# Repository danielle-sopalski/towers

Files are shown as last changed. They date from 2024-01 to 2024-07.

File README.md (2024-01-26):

# Miniature, Modular, Indoor Grow Towers

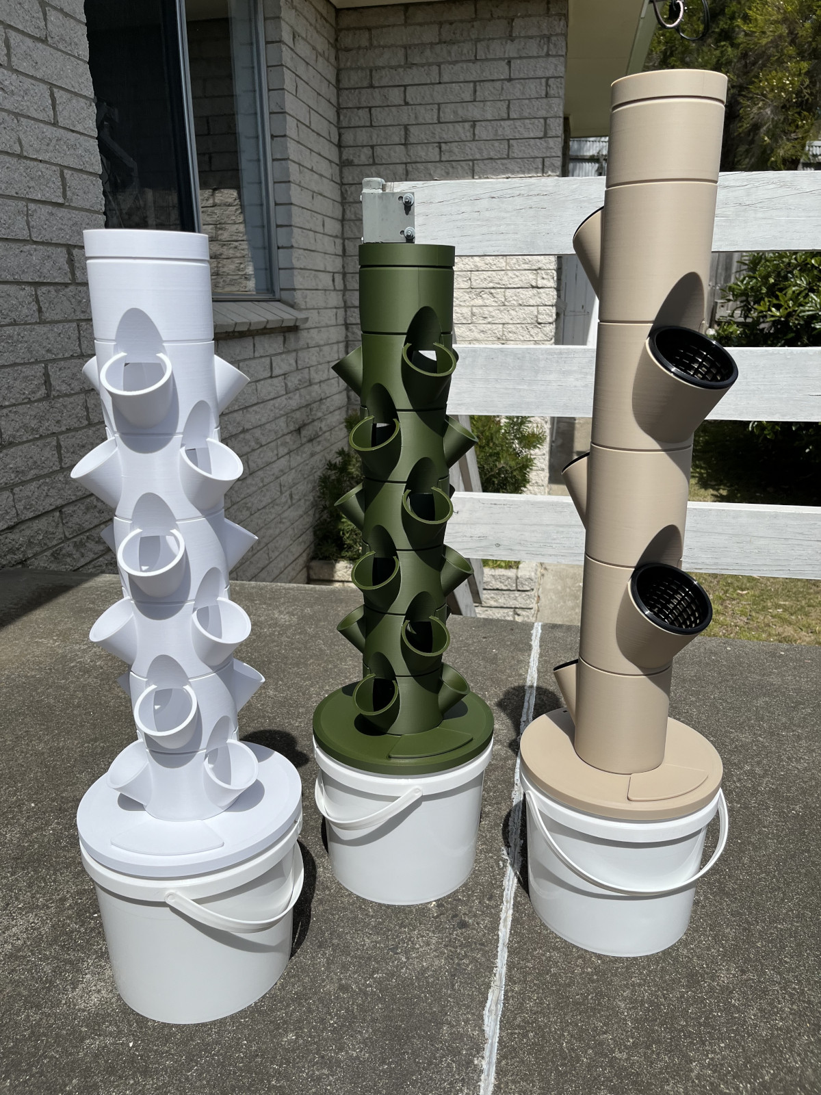
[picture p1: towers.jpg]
Image of three grow towers


## What is this?

These are hydroponic[^1] grow towers! The concept isn't new, and it's pretty straightforward: Instead of planting in soil, you plant in a loose medium like perlite or coco peat. Rather than the plants deriving nutrients from the growing medium, nutrients are dissolved in water, and that water is circulated through the system to deliver moisture and nutrients to the plants' roots. Because the water is recirculated and delivered directly to plants' roots, grow towers can be extremely water-efficient! Because nutrients are dissolved in the water itself, it's easy to control exactly what you put into the system, which means you can tailor it to the needs of whatever you've planted.

That said, I'm only a novice gardener, so I take a more simple approach: I use a general-purpose nutrient solution for all of my grows, and it seems to work out great for things like herbs and tomatoes! Hydroponic gardening can be as in-depth or as straightforward as you want it to be; it can be easy to start, and the complexity of the hobby can grow alongside your level of experience. :)

All of the parts in this project are designed to be 3D-printable without supports, and they're modular, meaning you can choose how many "planter" modules to put together to build your tower.

The planter modules come in two varieties: modules which fit a single 80mm net-pot per module; and modules which fit three 50mm net-pots per module. These net pots are easy to find at your local hydroponics shop or online if you don't have a shop nearby. For most herbs, lettuces, and even fruiting vegetables like tomatoes and peas, I recommend starting with the 50mm modules. Whereas you would normally need to use pots large enough to contain a plant's entire root system, net pots are designed to allow the root system to grow beyond the pot and down into the tower itself, so as long as a plant's base can fit in the diameter of the pot, you're golden!

[^1]: Well, technically, they could be called *aeroponic* grow towers. The best distinction I've heard between hydroponics and aeroponics is that if the roots are exposed to air, it's an aeroponic system. In theory, you could rig up one of these towers with some 4mm micro sprays or the like instead of the provided showerhead -- or you could even forego using a pump entirely and instead place a fog generator in the reservoir to experiment with fogponics! -- but I haven't tried it myself.

## What can I grow in these?

Pretty much anything except root vegetables! Lettuces, herbs, and peas are an easy place to start. Tomatoes are pretty easy too! It could even be fun to grow ornamentals in the towers, but my primary goal is to get people growing their own food.

## How do I get started? What do I need?

First things first: **Talk to the folks at your local hydroponics shop.** They're going to know way, *way* more than me about hydroponics and about growing plants in general. They'll be able to recommend nutrient solutions, pH buffers, and tools. **More importantly, they'll likely be able to advise you about hydroponics safety.** Not only does hydroponics involve the use of some simple chemicals like acidic and alkaline solutions for balancing pH, but a hydroponics system improperly tended to can become host to unwanted pathogens. The following advice is **general** in nature.

### To get started, you'll need a few items outside of the tower itself:
#### Non-printable components:
* A submersible pump to sit in the tower reservoir.[^2] I use [Aqua One Maxi 103](https://aquaone.com.au/2015-04-16-04-47-04/filtration/pumps-2/item/2702-11321-11322-11323-11324-11325-11326) pumps in my towers, but your hydroponics shop can advise you. You'll need to compare the height of your tower to the pump's **maximum head height.** If your tower is taller than that head height, your pump will struggle to push water to the top! If the maximum head height is significantly *higher* than the height of your tower, you may end up with too much water pressure for the system to handle.
* An outlet timer to switch your pump on and off automatically.[^2] I recommend a cycle of 15 minutes on, then one hour off.
* A way to adapt your pump's outlet to 13mm tubing.
* A length of 13mm tubing equal to the distance from your pump's outlet to shower head inlet about halfway up the "chimney module" -- that's the module at the top into which the shower head is inserted.
* A bucket to serve as your system's reservoir. At the moment, the design suits only Ayva brand 5L buckets. These are an Australian make of bucket commonly available individually at Bunnings Warehouse under the brand name [Handy Pail](https://www.bunnings.com.au/handy-pail-5l-plastic-pail-with-lid_p4475883). My hope is that as people take notice of the project, folks will contribute revised bucket lid designs suitable for buckets available in countries other than Australia.
* Either 50mm or 80mm net pots. While I haven't included a design for those in this project, there are actually a [ton of available printable versions](https://thangs.com/search/net%20pot?scope=all)!

#### Tools:
* A pH meter is really important to make sure your nutrient solution is in the right pH range for your plants.
* Eyedroppers are a great way to dispense the small amounts of buffer needed to balance your nutrient solution's pH.
* A small graduated cylinder or conical medicine measure -- that's what I use -- is perfect for measuring out concentrated nutrient solution for mixing. Conical medicine measures can be found at chemists (pharmacies), and they're very inexpensive.

#### Consumables:
* Concentrated nutrient solution
* Hydroponics acid, often called "pH down"[^3]
* Hydroponics base, often called "pH up"[^3]
* It's best practice -- many would say a must -- to use a cleaning agent to sterilize your tower as much as possible before planting and filling with nutrient solution. The folks at your local hydroponics shop can advise you.
* A planting medium. I prefer perlite for its excellent drainage, but coco peat is a perfectly valid option too. Your local hydroponics shop can advise you.
* Water of course!
* Your local hydroponics shop can advise you about other additives to help keep your system healthy.

#### Optional stuff if you wanna go wild:
* A grow lamp
* A grow tent
* A little fan to help air circulate through your plants
* A trellis or trainer and twine is quite helpful for plants like peas and tomatoes.

[^2]: These towers **can** leak. Be sure to place them such that any leaks wouldn't reach electrical outlets or electrical devices.
[^3]: Remember, it's of paramount importance to exercise caution and wear appropriate personal protective equipment when handling harsh chemicals such as (but not limited to) acids, bases, and oxidizing agents.

### How many modules should I use?
I recommend starting with just one or two of the 50mm planter modules. Each 50mm module will give you three net-pot receptacles, and you may be surprised by how much water your chosen plants will consume once they reach a decent size. One of the limitations of these towers as they are is the reservoir size. At 5L, the reservoir can be drained pretty quickly by a fully populated, reasonably tall tower! However, I've also provided what I'm calling a ["bulkhead fitting"](https://github.com/danielle-sopalski/towers/blob/main/bucket%20lid/Bulkhead%20for%20Larger%20Systems.step), which can be fastened with screws to larger reservoir lids as an alternative to the printable bucket lid for those who want to try building larger systems (or even systems with multiple towers attached to the same large reservoir).

### Once you have everything you need, be sure to check out the [assembly manual](https://github.com/danielle-sopalski/towers/blob/main/manual/main.pdf). It's not yet complete -- a couple of sections are filled with *Lorem ipsum* -- but it contains complete assembly instructions, and I've put a lot of effort into making wireframe diagrams that I hope will help!

## Printing Recommendations

The towers were designed to be printed by my Bambu Lab P1S printer, but they should be printable on any decent FDM printer, maybe with some tweaking of clearances.

**All parts are designed to be printed without supports.** Examples of recommended print orientation can be found in the example 3MF files. When printed with the recommended orientation and on a print surface such as textured PEI, the result should be a nice, textured finish on all upward-facing surfaces of the assembled tower. :)

For parts with little surface area contacting the print bed, eg planter modules, an inner brim can be used to promote bed adhesion.

I recommend using PLA+ and **strongly** recommend you find **food-grade** filament to print with.[^4]

Generally, I've been printing with:
* 0.28mm layer height
* 0.4mm nozzle, though 0.6mm or larger certainly isn't out of the question!
* 3 wall loops for planter modules; 6 wall loops for the bucket lid
* 3 top and bottom shell layers
* Rectilinear top and bottom surface pattern for the bucket lid; concentric top and rectilinear bottom surface pattern for the planter modules, bucket lid cap, bucket lid lock-ring, bucket lid cable glands, tower chimney, chimney lid
* **No supports**
* Gyroid infill, 15%

[^4]: Remember: Just because your filament is food-grade doesn't mean your printer or finished prints are!

## Intention

This is a project I've been working on for a little while with the intention, up until now, of starting a small business centered around hyper-local manufacturing of goods. The hope was to promote the idea of "garage factories," tiny print farms in people's spare space serving local communities with goods that would otherwise need to be sourced from large factories far away. Truth be told, though, I'm not a business person, and I don't think I want to move forward with it myself -- or at least not alone -- so I'm opening the project in the hope that others will see value in it and contribute their time and abilities to making it better than I ever could by myself.

My hope now is that folks will go about producing these grow towers for their own local communities, promoting both hyper-local manufacturing and home-grown produce.

## What's Here

These are small, modular, indoor, hydroponic grow towers made to sit in a living room or by a window. Included in the repo are:
* A variant with one 80mm net-pot receptacle per module: Fusion 360, STEP
* A variant with three 50mm net-pot receptacles per module: Fusion 360, STEP
* A mostly-complete (though certainly not perfectly written) user manual: PDF, (badly written) LaTeX; A4 format as well as A5 booklet format
* Wireframe diagrams of all parts and assembly steps: SVG
* 3MF files of all parts offering example printing parameters.

## What Needs to Be Done

A number of things need improvement:
* The manual needs an introduction, a sensible list of precautions, cleaning and maintenance recommendations, and general proofreading and refinement.
* The Fusion 360 files need to be cleaned up. I'm bad at keeping things organized while I work.
* **The current design only suits a common Australian brand of 5L bucket.** I'd love it if folks could contribute revised versions that suit buckets available in other parts of the world.
* We need a good open-source license that allows individuals to freely produce and sell these towers while excluding large manufacturers, corporations, and the wealthy. For now, I'm opting for the [Creative Commons Attribution-NonCommercial-ShareAlike 4.0 International license](https://creativecommons.org/licenses/by-nc-sa/4.0/).

### Models from this project are also published to [Thangs](https://thangs.com/designer/danielle.sopalski/3d-model/Dani%27s%20Miniature%20Grow%20Towers-995522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) and [Thingiverse](https://www.thingiverse.com/thing:6444781).

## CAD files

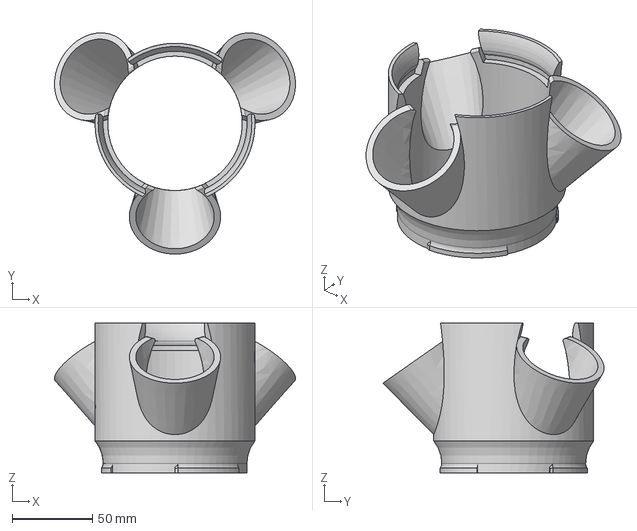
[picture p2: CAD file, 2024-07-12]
50mm/50mm Planter Base Module.step
150.6 x 138.2 x 93.6 mm

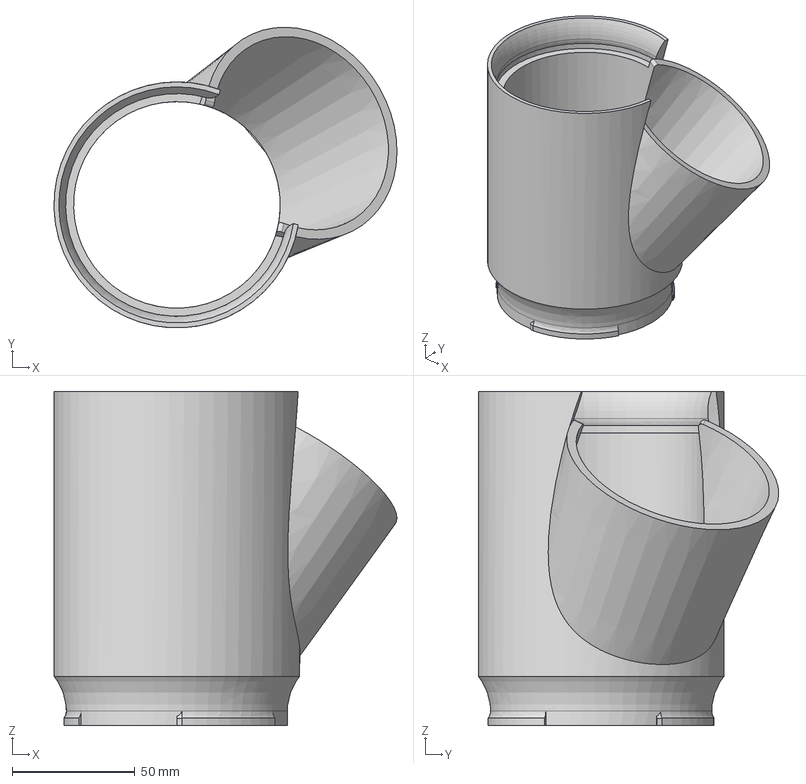
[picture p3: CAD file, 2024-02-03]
80mm/80mm Planter Base Module.step
139.5 x 122.2 x 135.9 mm

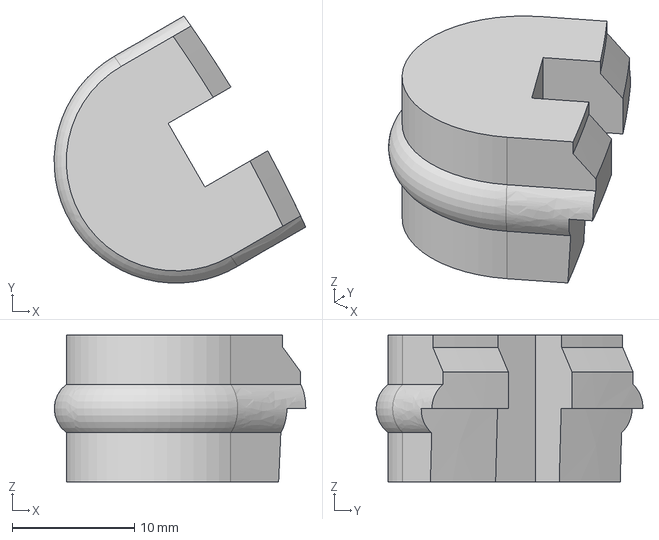
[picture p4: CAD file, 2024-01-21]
bucket lid/Ayva 5L Lock-Ring Pail Lid Cable Gland.step
20.5 x 21.8 x 12.0 mm

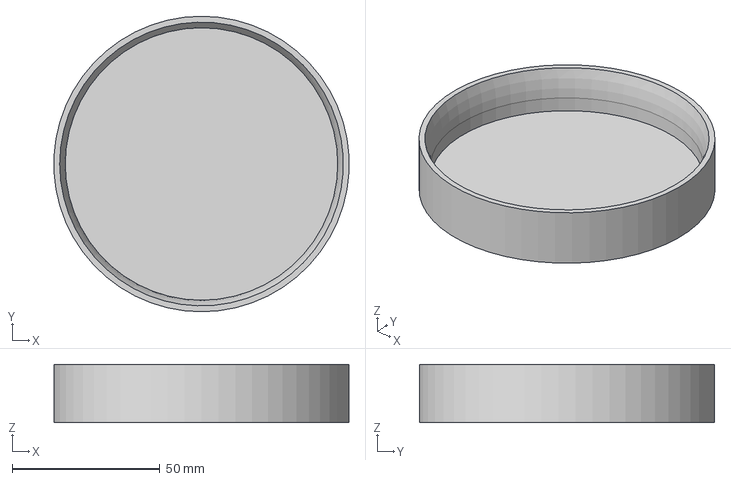
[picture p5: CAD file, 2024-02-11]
chimney lid/Chimney Lid.step
99.8 x 100.0 x 19.6 mm

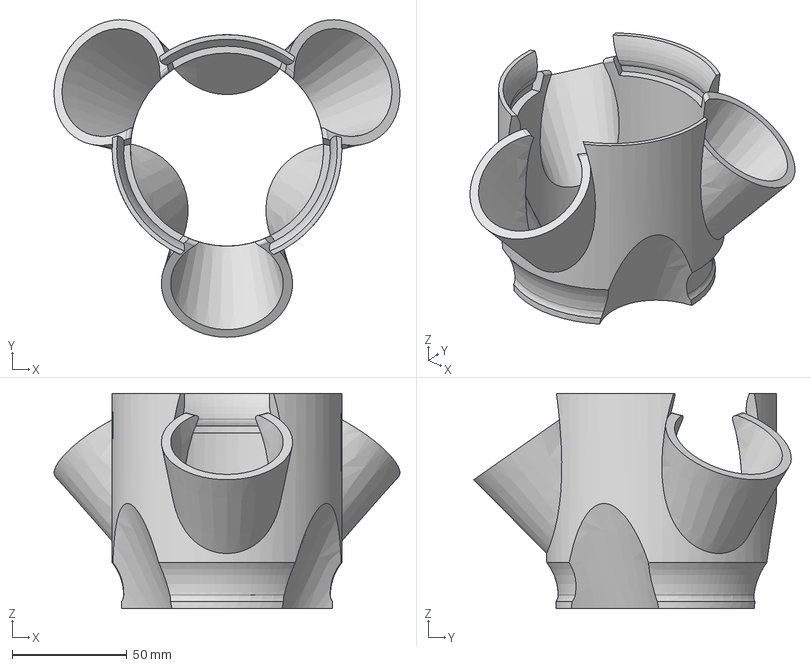
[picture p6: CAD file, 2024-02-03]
50mm/50mm Planter Module.step
150.6 x 138.2 x 93.6 mm

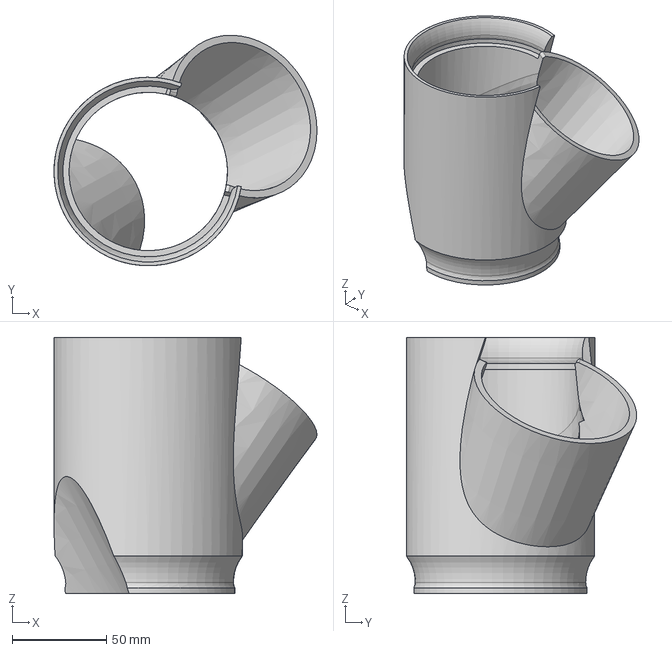
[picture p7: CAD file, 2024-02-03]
80mm/80mm Planter Module.step
139.5 x 122.2 x 135.9 mm

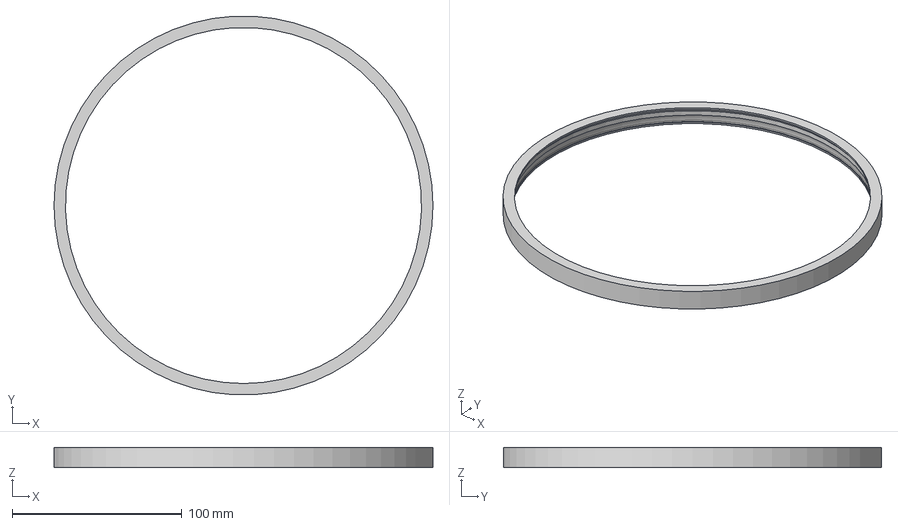
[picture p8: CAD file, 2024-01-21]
bucket lid/Ayva 5L Lock-Ring Pail Lid Lock-Ring.step
223.5 x 223.2 x 12.0 mm

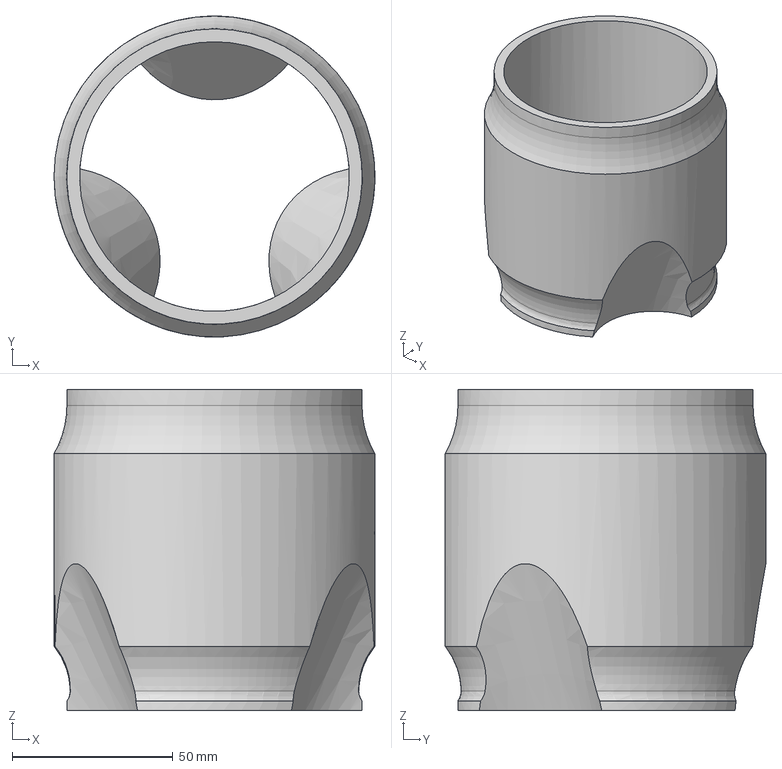
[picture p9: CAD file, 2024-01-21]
50mm/50mm Chimney Module.step
100.0 x 100.0 x 100.0 mm

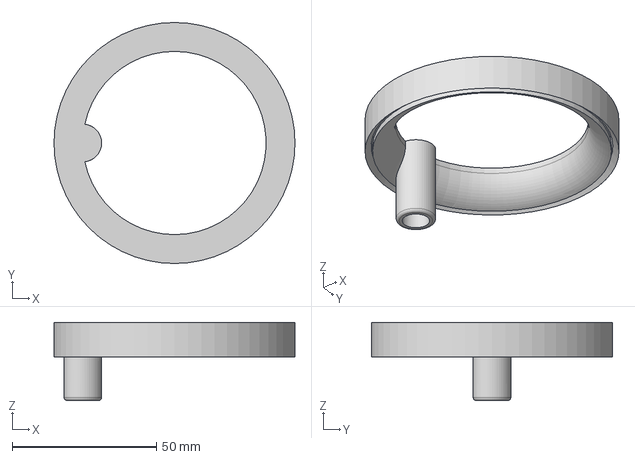
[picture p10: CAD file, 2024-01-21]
80mm/80mm Shower Head.step
83.4 x 83.4 x 27.0 mm

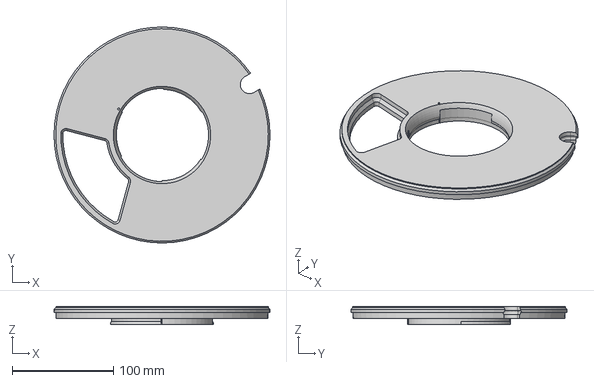
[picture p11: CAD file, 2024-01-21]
bucket lid/Ayva 5L Lock-Ring Pail Lid.step
213.3 x 213.3 x 18.0 mm

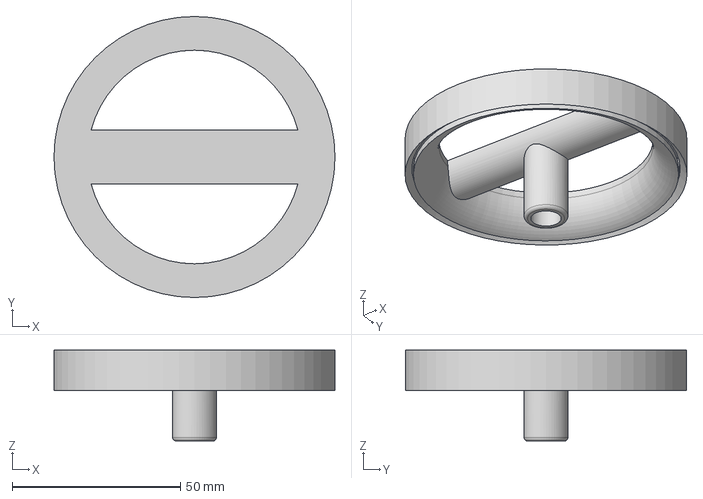
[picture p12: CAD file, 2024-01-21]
50mm/50mm Shower Head.step
83.4 x 83.4 x 27.0 mm

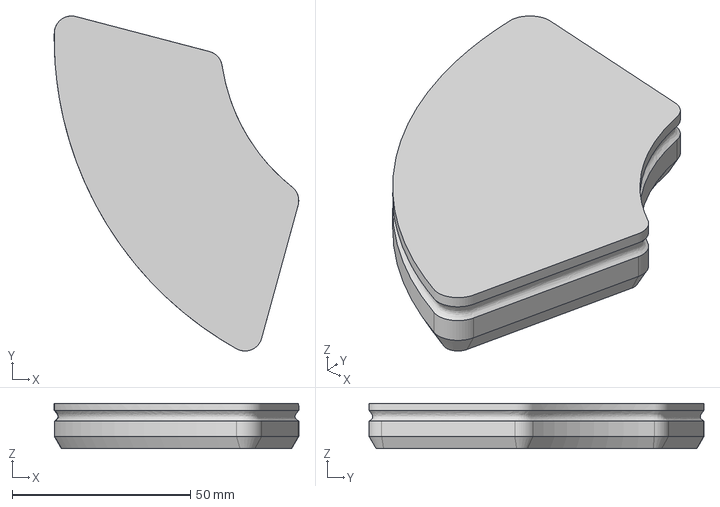
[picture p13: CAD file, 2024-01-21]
bucket lid/Ayva 5L Lock-Ring Pail Lid Cover.step
68.6 x 94.0 x 12.8 mm

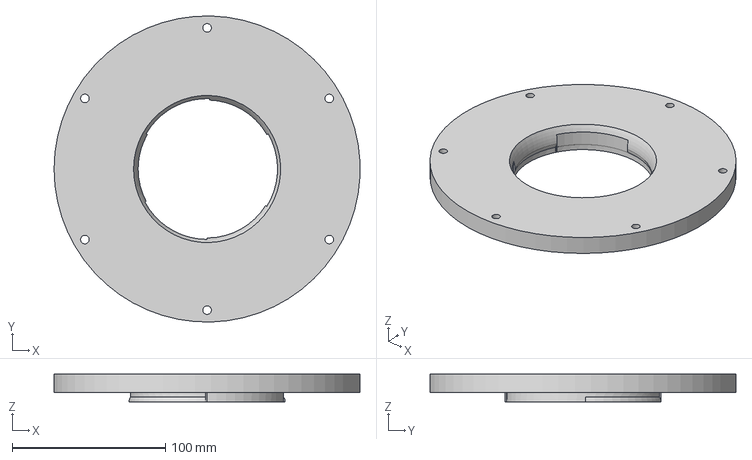
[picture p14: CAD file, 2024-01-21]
bucket lid/Bulkhead for Larger Systems.step
199.9 x 199.9 x 18.0 mm

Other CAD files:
80mm/80mm Chimney Module.step
50mm/3mf/50mm Chimney Module.3mf
50mm/3mf/50mm Planter Base Module.3mf
50mm/3mf/50mm Planter Module.3mf
50mm/3mf/50mm Shower Head.3mf
50mm/Tower 50mm.f3z
80mm/3mf/80mm Chimney Module.3mf
80mm/3mf/80mm Planter Base Module.3mf
80mm/3mf/80mm Planter Module.3mf
80mm/3mf/80mm Shower Head.3mf
80mm/Tower 80mm.f3z
bucket lid/3mf/Ayva 5L Lock-Ring Pail Lid Cable Gland.3mf
bucket lid/3mf/Ayva 5L Lock-Ring Pail Lid Cover.3mf
bucket lid/3mf/Ayva 5L Lock-Ring Pail Lid Lock-Ring.3mf
bucket lid/3mf/Ayva 5L Lock-Ring Pail Lid.3mf
chimney lid/3mf/Chimney Lid.3mf

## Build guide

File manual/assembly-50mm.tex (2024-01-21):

\subsection{Parts}

\begin{center}
    \begin{minipage}{0.3\textwidth}
        \centering
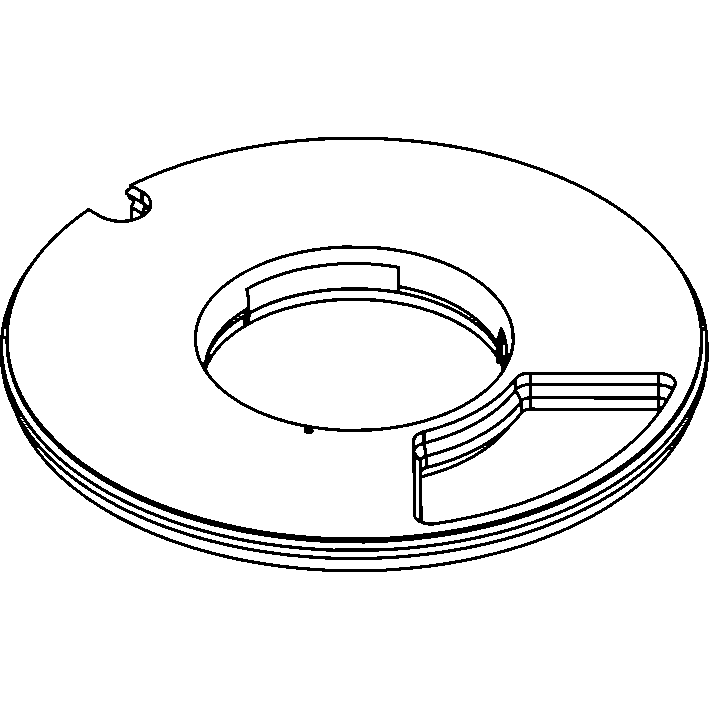
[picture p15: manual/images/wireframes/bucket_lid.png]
        
        \captionof*{figure}{1x Bucket Lid}
    \end{minipage}
    \hfill
    \begin{minipage}{0.3\textwidth}
        \centering
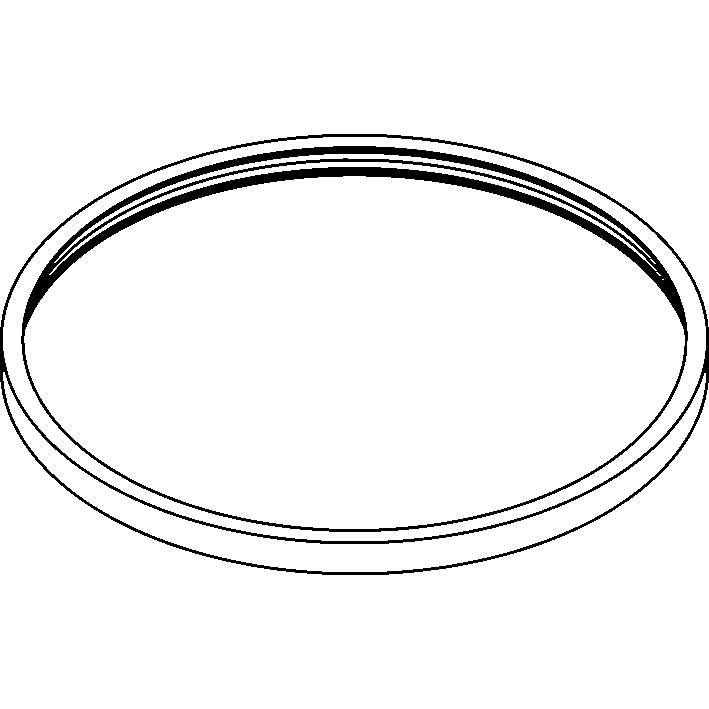
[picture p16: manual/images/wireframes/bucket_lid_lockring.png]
        
        \captionof*{figure}{1x Bucket lid lock-ring}
    \end{minipage}
    \hfill
    \begin{minipage}{0.3\textwidth}
        \centering
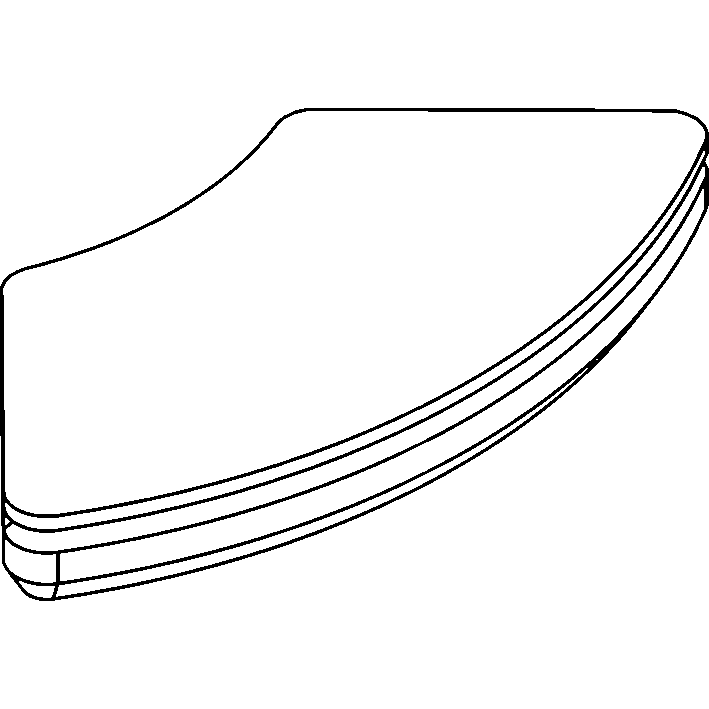
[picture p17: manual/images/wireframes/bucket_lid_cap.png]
        
        \captionof*{figure}{1x Bucket lid cap}
    \end{minipage}

    \vspace{8pt}
    \rule{\textwidth}{0.5pt}
    \vspace{2pt}

    \begin{minipage}{0.3\textwidth}
        \centering
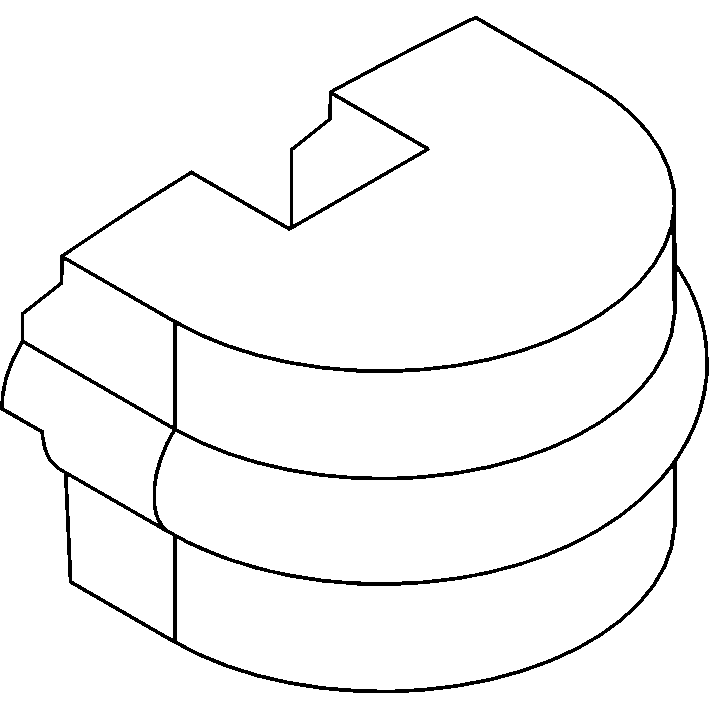
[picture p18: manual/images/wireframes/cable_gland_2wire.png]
        
        \captionof*{figure}{1x Two-wire cable gland}
    \end{minipage}
    \hfill
    \begin{minipage}{0.3\textwidth}
        \centering
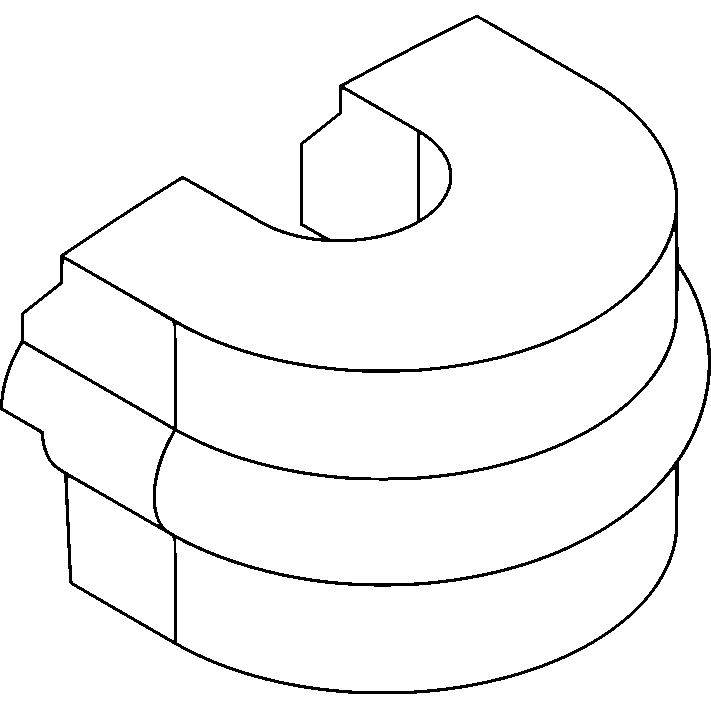
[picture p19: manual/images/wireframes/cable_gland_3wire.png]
        
        \captionof*{figure}{1x Three-wire cable gland}
    \end{minipage}
    \hfill
    \begin{minipage}{0.3\textwidth}
        \centering
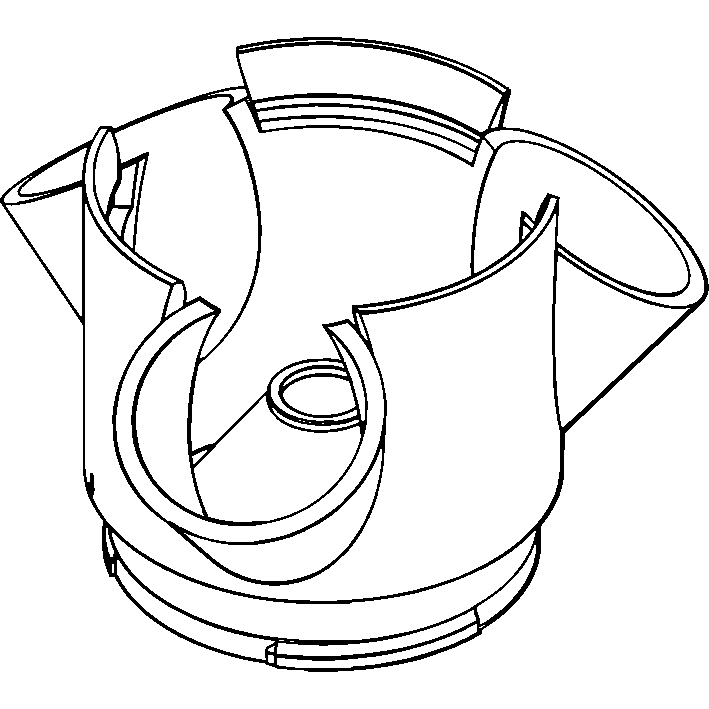
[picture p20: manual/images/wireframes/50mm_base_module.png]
        
        \captionof*{figure}{1x Twist-lock base module}
    \end{minipage}

    \vspace{8pt}
    \rule{\textwidth}{0.5pt}
    \vspace{2pt}

    \begin{minipage}{0.3\textwidth}
        \centering
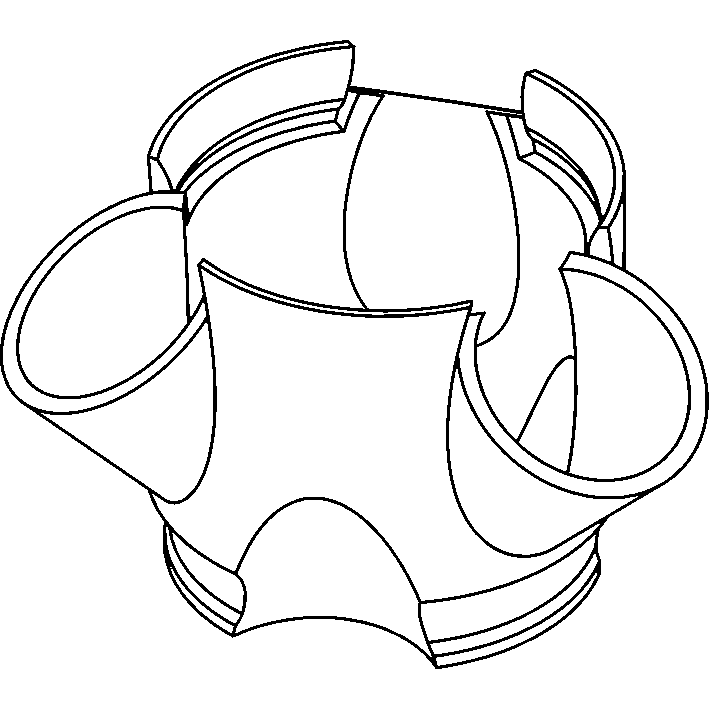
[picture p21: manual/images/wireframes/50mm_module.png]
        
        \captionof*{figure}{5x Snap-fit module}
    \end{minipage}
    \hfill
    \begin{minipage}{0.3\textwidth}
        \centering
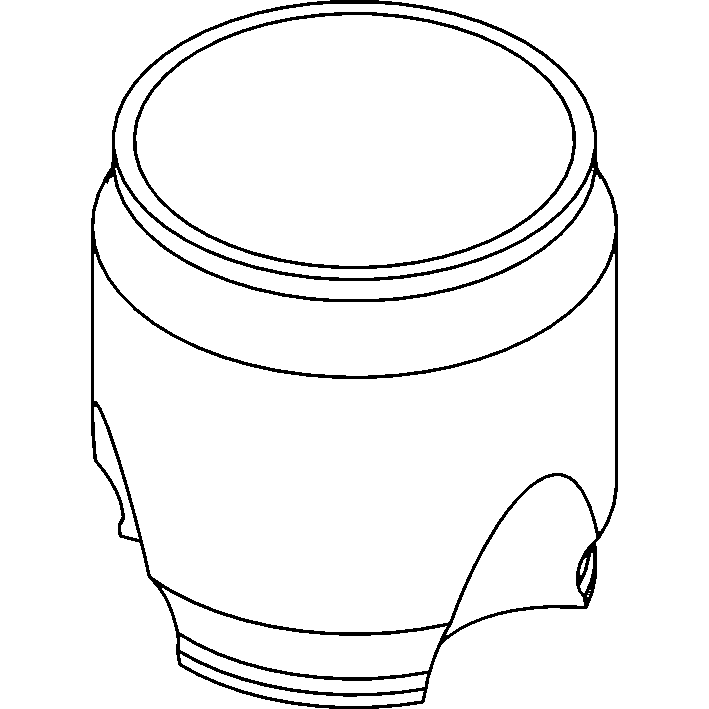
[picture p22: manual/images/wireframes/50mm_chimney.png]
        
        \captionof*{figure}{1x Chimney module}
    \end{minipage}
    \hfill
    \begin{minipage}{0.3\textwidth}
        \centering
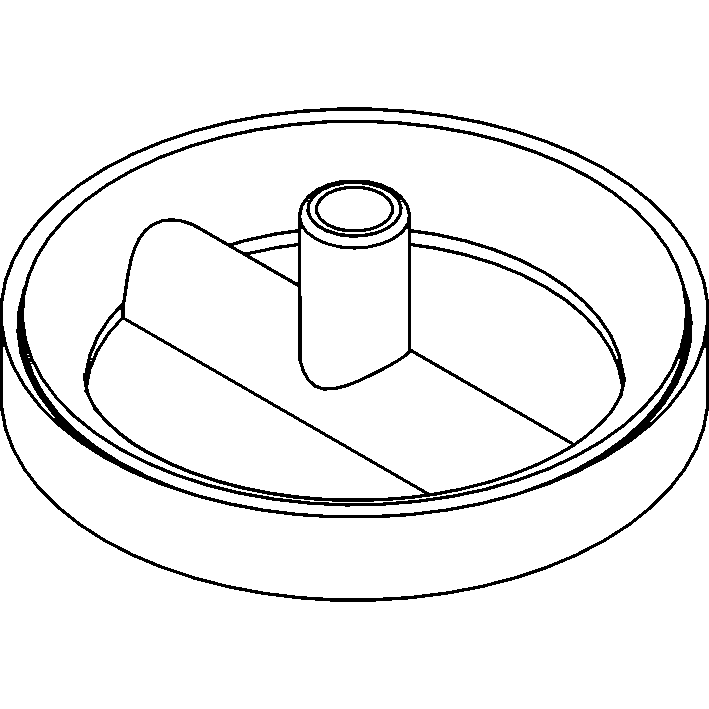
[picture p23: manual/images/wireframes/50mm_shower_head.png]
        
        \captionof*{figure}{1x Shower head}
    \end{minipage}

    % \vspace{8pt}
    % \rule{\textwidth}{0.5pt}
    % \vspace{2pt}

    \begin{minipage}{0.3\textwidth}
        \centering
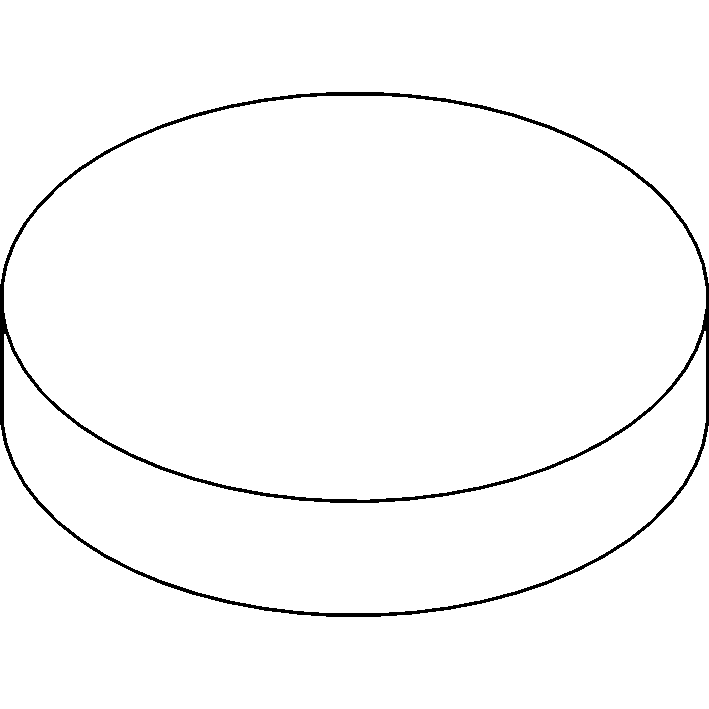
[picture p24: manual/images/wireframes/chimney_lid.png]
        
        \captionof*{figure}{1x Chimney lid}
    \end{minipage}
    \hfill
    \begin{minipage}{0.3\textwidth}
        \centering
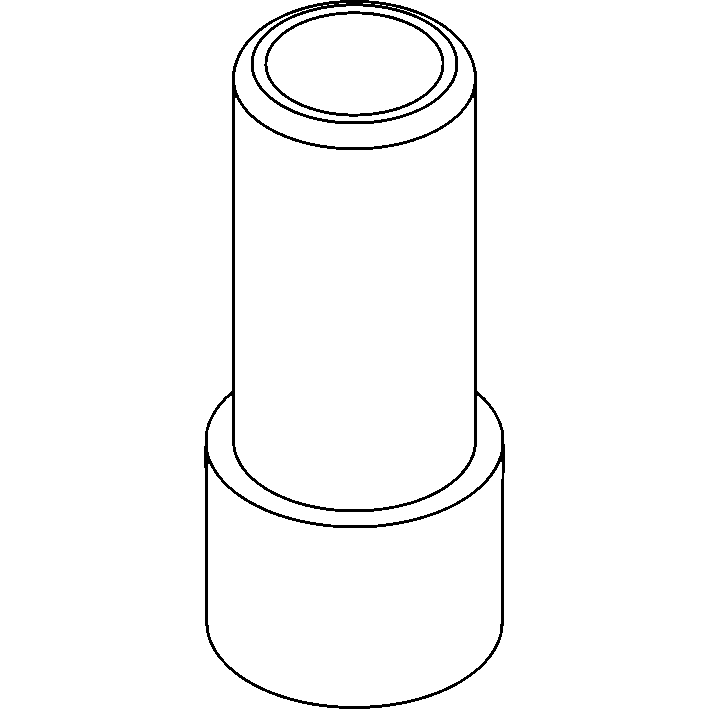
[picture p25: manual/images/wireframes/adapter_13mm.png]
        
        \captionof*{figure}{1x 13mm hose adapter}
    \end{minipage}
    \hfill
    \begin{minipage}{0.3\textwidth}
        \centering
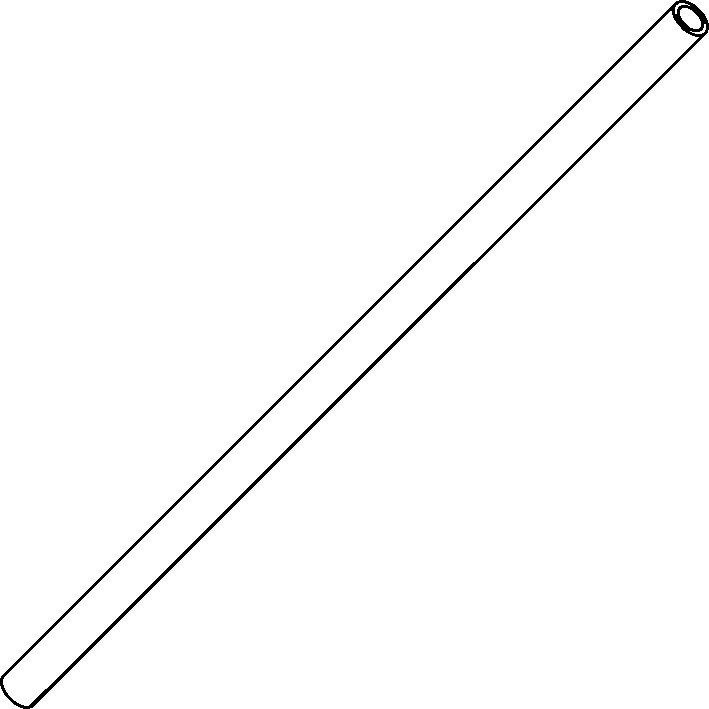
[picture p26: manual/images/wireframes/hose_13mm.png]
        
        \captionof*{figure}{1x 13mm Hose}
    \end{minipage}

    \vspace{8pt}
    \rule{\textwidth}{0.5pt}
    \vspace{2pt}

    \begin{minipage}{0.3\textwidth}
        \centering
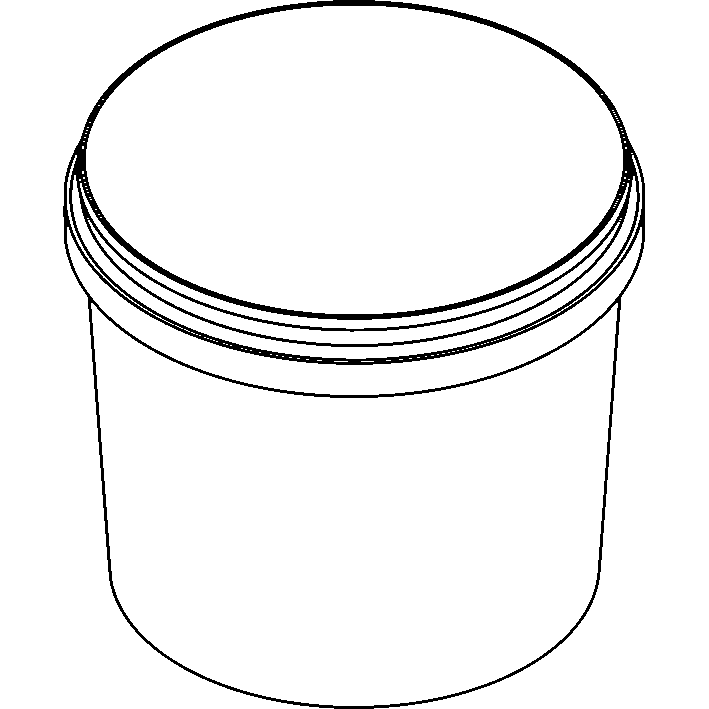
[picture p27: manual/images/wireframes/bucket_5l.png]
        
        \captionof*{figure}{1x 5L Bucket}
    \end{minipage}
\end{center}

\clearpage

\setlength{\intextsep}{15.0pt plus 0.0pt minus 0.0pt}
\setlength{\floatsep}{10.0pt plus 0.0pt minus 0.0pt}
\setlength{\textfloatsep}{15.0pt plus 0.0pt minus 0.0pt}
\setlength{\belowcaptionskip}{-30.0pt}

\subsection{Assembly}

\begin{enumerate}

\item Align the arrow at the base of the \textbf{twist-lock base module} with the arrow on the top of the \textbf{bucket lid}. Carefully insert the base of the module into the hole in the center of the bucket lid when the arrows are aligned.

\item Once the \textbf{twist-lock base module} is inserted into the \textbf{bucket lid}, twist the module clockwise until you feel it stop. \textbf{Do not twist past this point.}

\begin{figure}[h]
    \centering
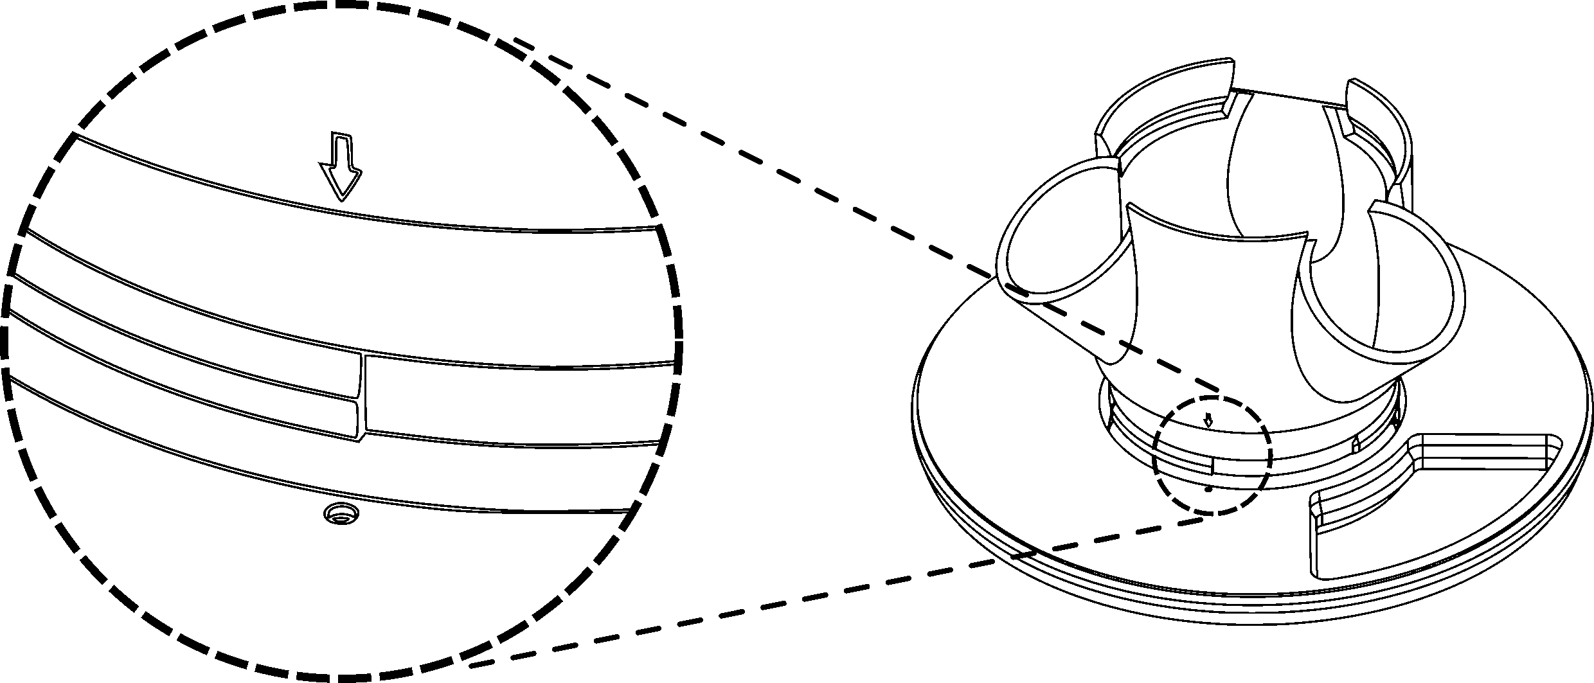
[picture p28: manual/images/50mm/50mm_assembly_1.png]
    
    \caption*{}
    \label{fig:50mm-one}
\end{figure}
\begin{figure}[h!]
    \centering
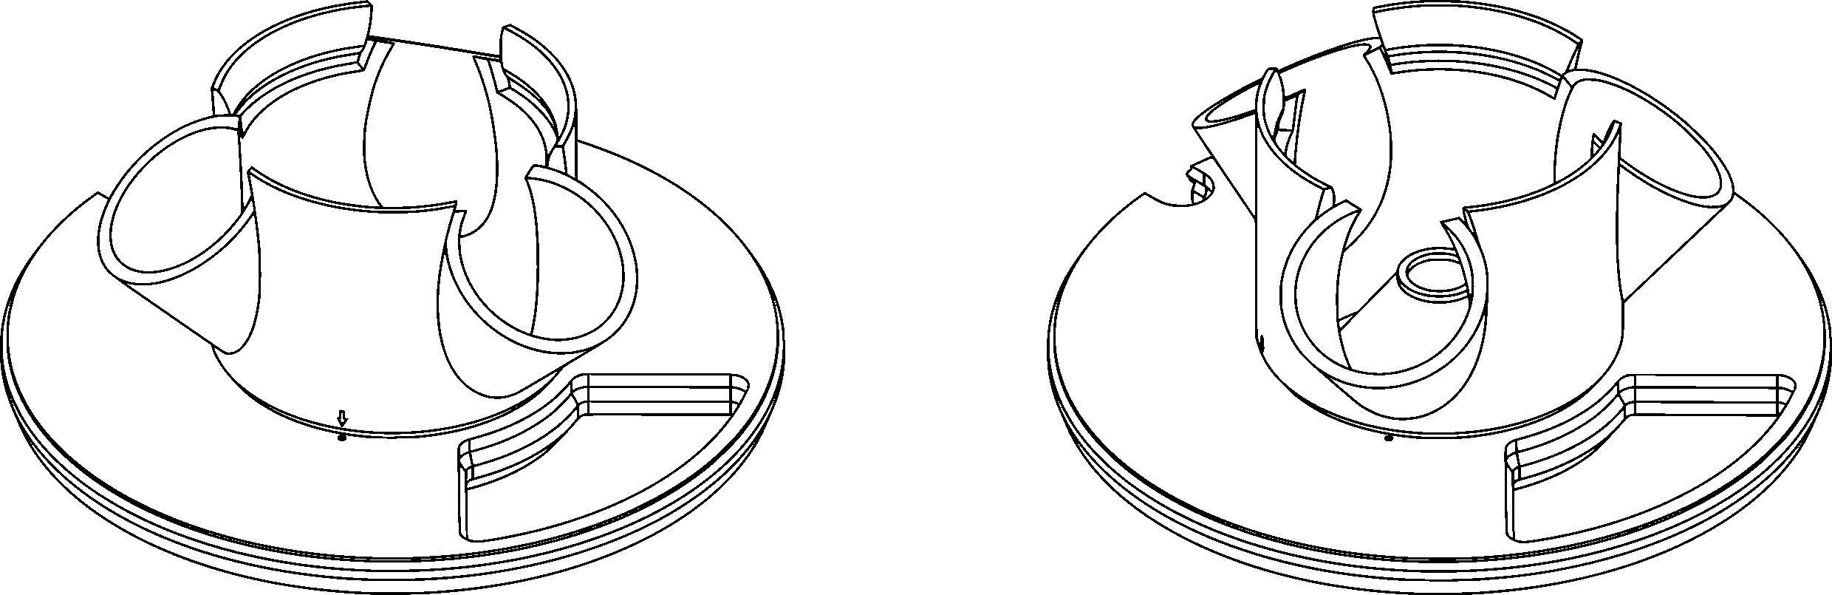
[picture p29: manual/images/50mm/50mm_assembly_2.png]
    
    \caption*{}
    \label{fig:50mm-two}
\end{figure}

\item Align the bottom of a \textbf{snap-fit module} with the top of the \textbf{twist-lock base module} so that the foot of the upper module fits into the receiver of the lower module, then gently push the upper module down until it snaps snugly together with the lower module.

\begin{figure}[h!]
    \centering
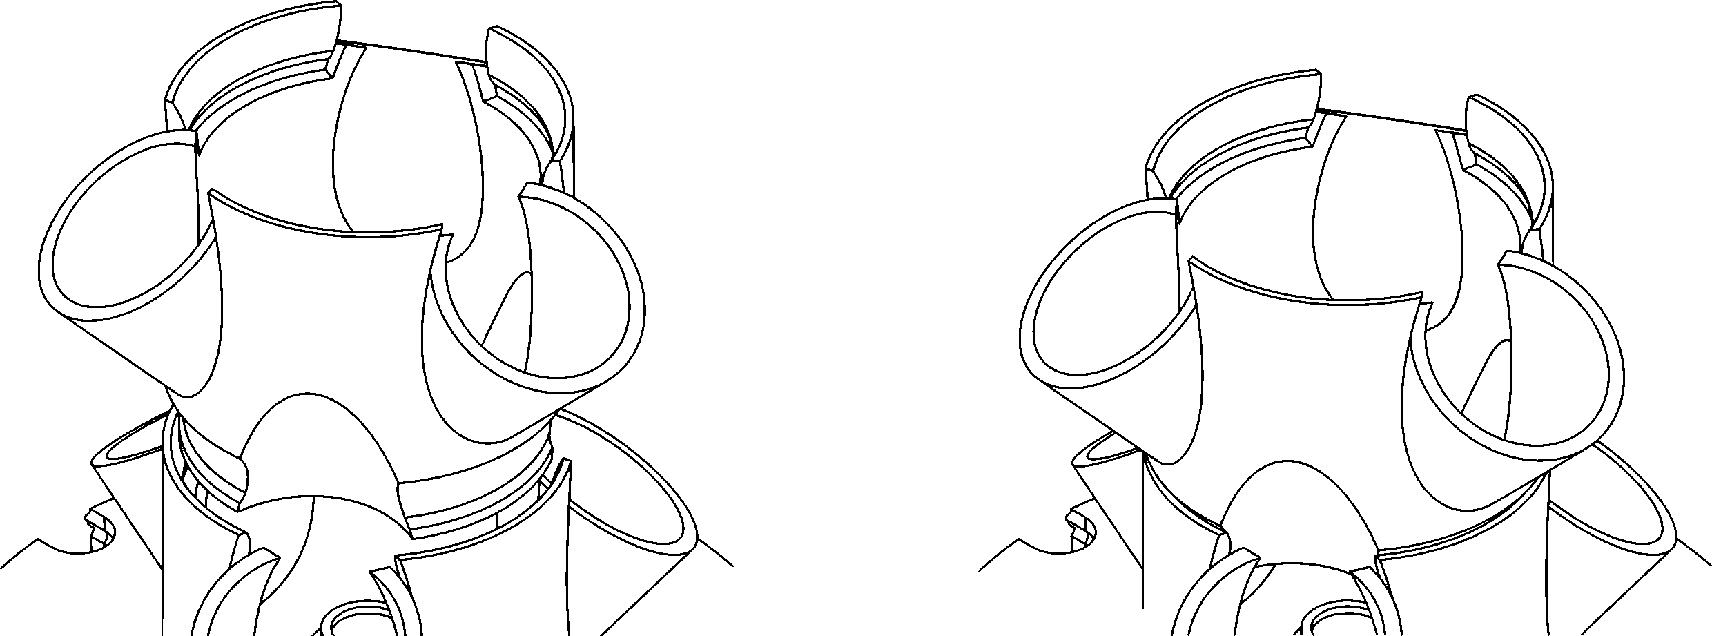
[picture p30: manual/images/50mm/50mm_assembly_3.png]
    
    \caption*{}
    \label{fig:50mm-three}
\end{figure}
\begin{figure}[h!]
    \centering
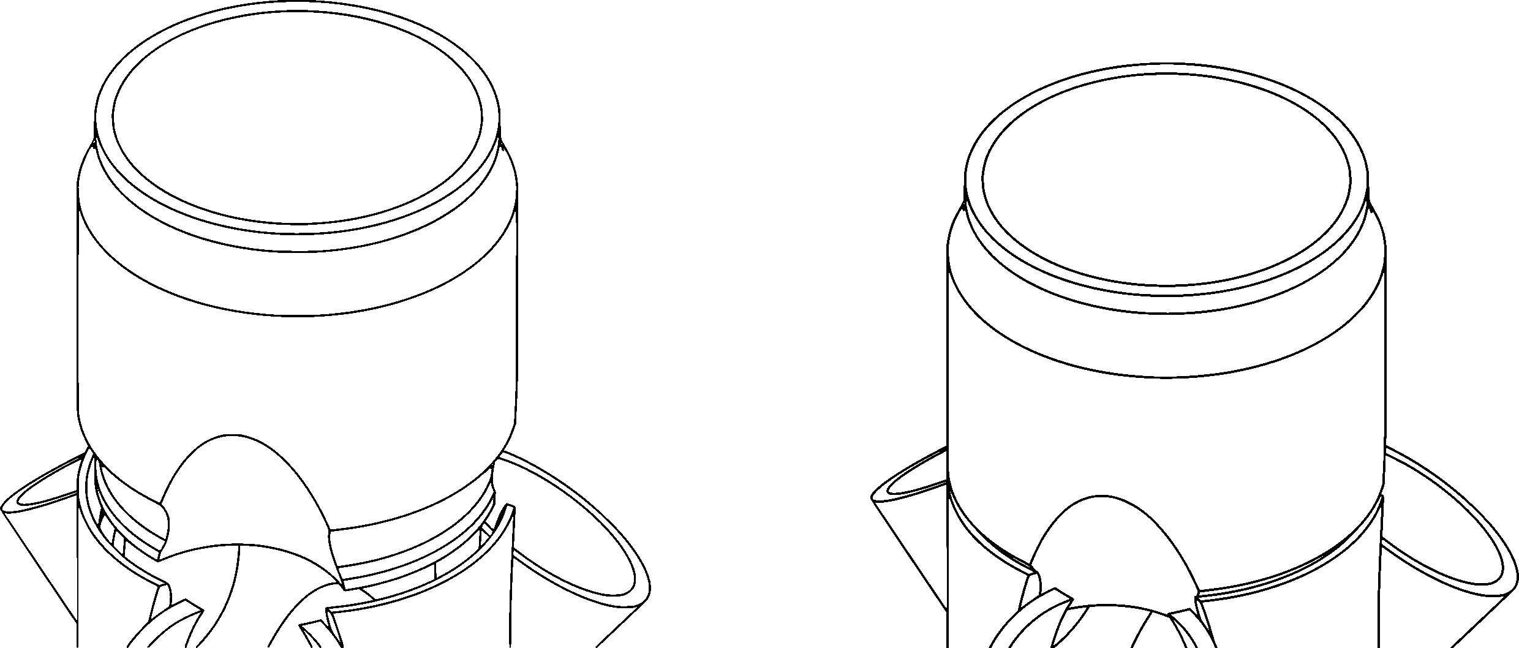
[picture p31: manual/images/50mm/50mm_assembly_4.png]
    
    \caption*{}
    \label{fig:50mm-four}
\end{figure}

\item Repeat step 3 with the remaining planter modules.

\item Using the same method, insert the \textbf{chimney module} into the snap-fit receiver of the topmost planter module.

\item Insert the water inlet of the \textbf{shower head} into one end of the \textbf{13mm hose}.

\begin{figure}[h!]
    \centering
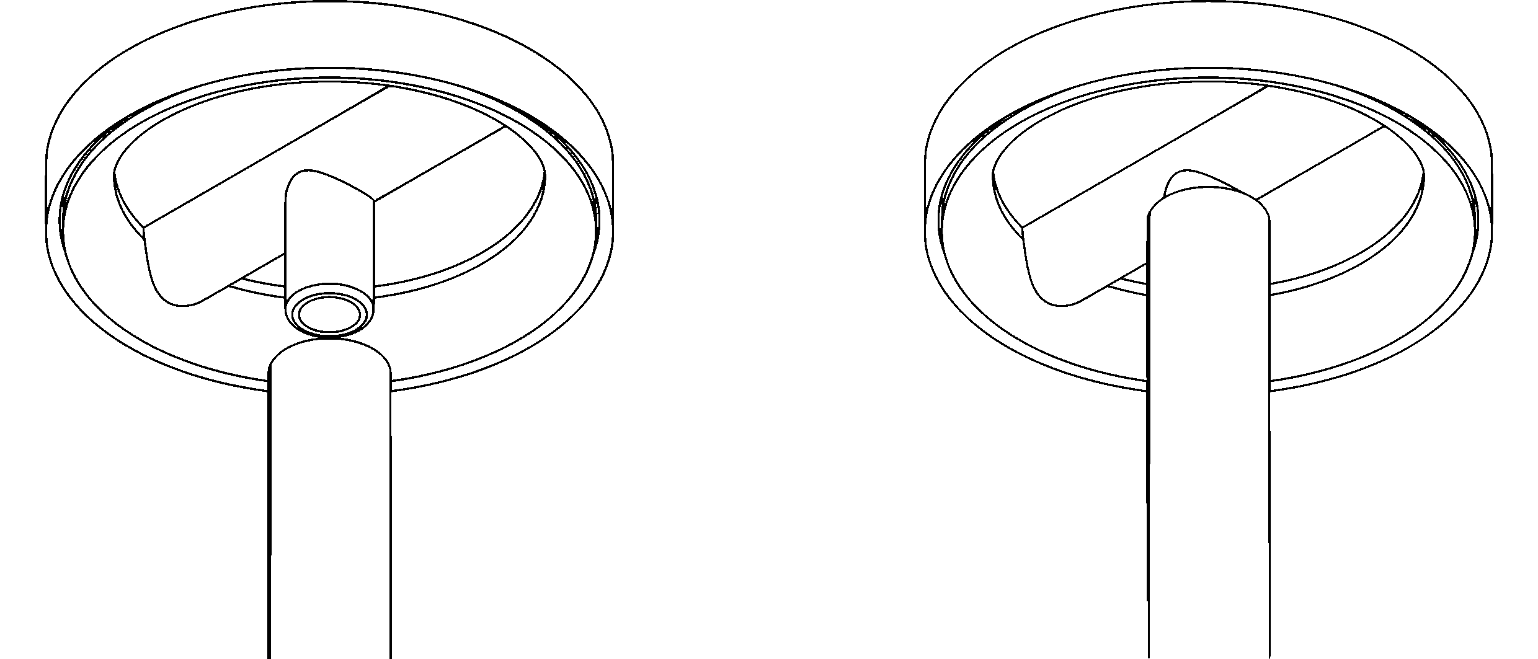
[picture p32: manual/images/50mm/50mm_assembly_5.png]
    
    \caption*{}
    \label{fig:50mm-five}
\end{figure}
\begin{figure}[h!]
    \centering
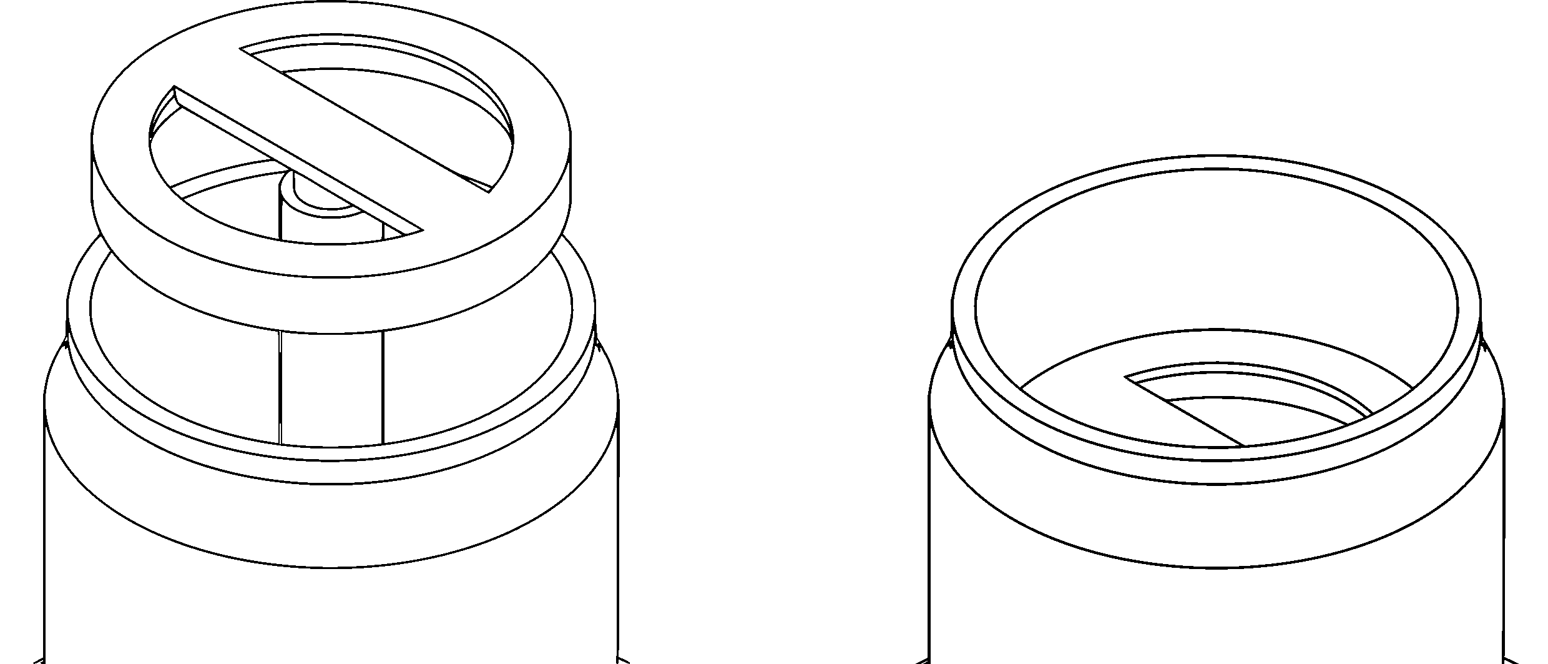
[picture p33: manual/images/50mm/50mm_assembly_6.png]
    
    \caption*{}
    \label{fig:50mm-six}
\end{figure}

\item Insert the opposite end of the \textbf{13mm hose} into the tower through the top of the \textbf{chimney module}, then insert the \textbf{shower head} into the top of the chimney module and push it down as far as it will go. Do not force the shower head further into the chimney module than it will go. The shower head is designed to fit snugly into the chimney module to aid the laminar flow of water over the inner wall of the tower, so \textbf{be careful not to angle the shower head as you insert it.}

\item Insert the appropriate \textbf{bucket lid cable gland} for your chosen pump's power cord into the cable gland receiver of the \textbf{bucket lid}. Be careful to ensure that the cable gland is oriented correctly, or the bucket lid won't sit properly on the bucket.

\begin{figure}[h!]
    \centering
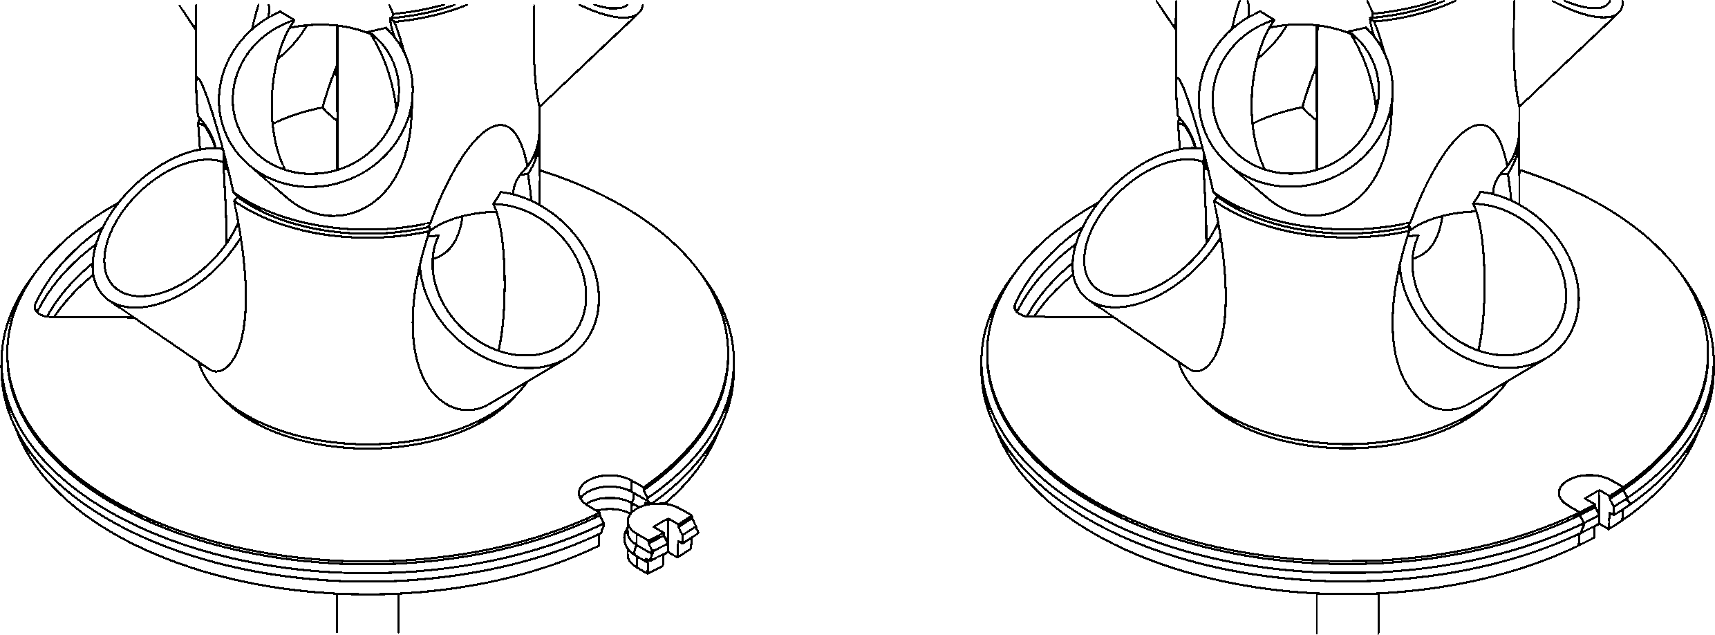
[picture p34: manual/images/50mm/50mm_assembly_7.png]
    
    \caption*{}
    \label{fig:50mm-seven}
\end{figure}

\item Place your \textbf{submersible pump} in the \textbf{5L bucket}.

\item If using an Aqua One 103 pump or other Aqua One pump with the same outlet, insert the 13mm end of the \textbf{13mm hose adapter} into the free end of the 13mm hose. If using a different pump, appropriate adapters will need to be provided by the user.

\item While holding the tower so that the bucket lid hovers just above the lip of the bucket, connect the free end of the 13mm hose to the outlet of the submersible pump. You may need to adjust the position of the pump in the bucket to ensure that the pump outlet aligns with the hose.

\item Lower the bucket lid onto the lip of the bucket, ensuring that the power cord of the pump is routed through the bucket lid cable gland. As the bucket lid is lowered, gently pull the shower head upward inside the chimney so that the hose is straightened but not taut.

\item Lower the \textbf{bucket lid lock-ring}, with its flat side facing upward, down over the top of the tower. Align the lock-ring with the edge of the bucket lid, then carefully push the lock-ring down into place around the bucket-lid. It may be easiest to work from one point on the lock-ring and around to the other side in both directions simultaneously with both thumbs.

\item Insert the \textbf{bucket lid cap}, with its flat side facing upward, into the cap opening in the bucket lid.

\item Place the \textbf{chimney lid}, with its flat side facing upward, on top of the tower chimney.

\begin{figure}[h]
    \centering
    \vspace{-10pt}
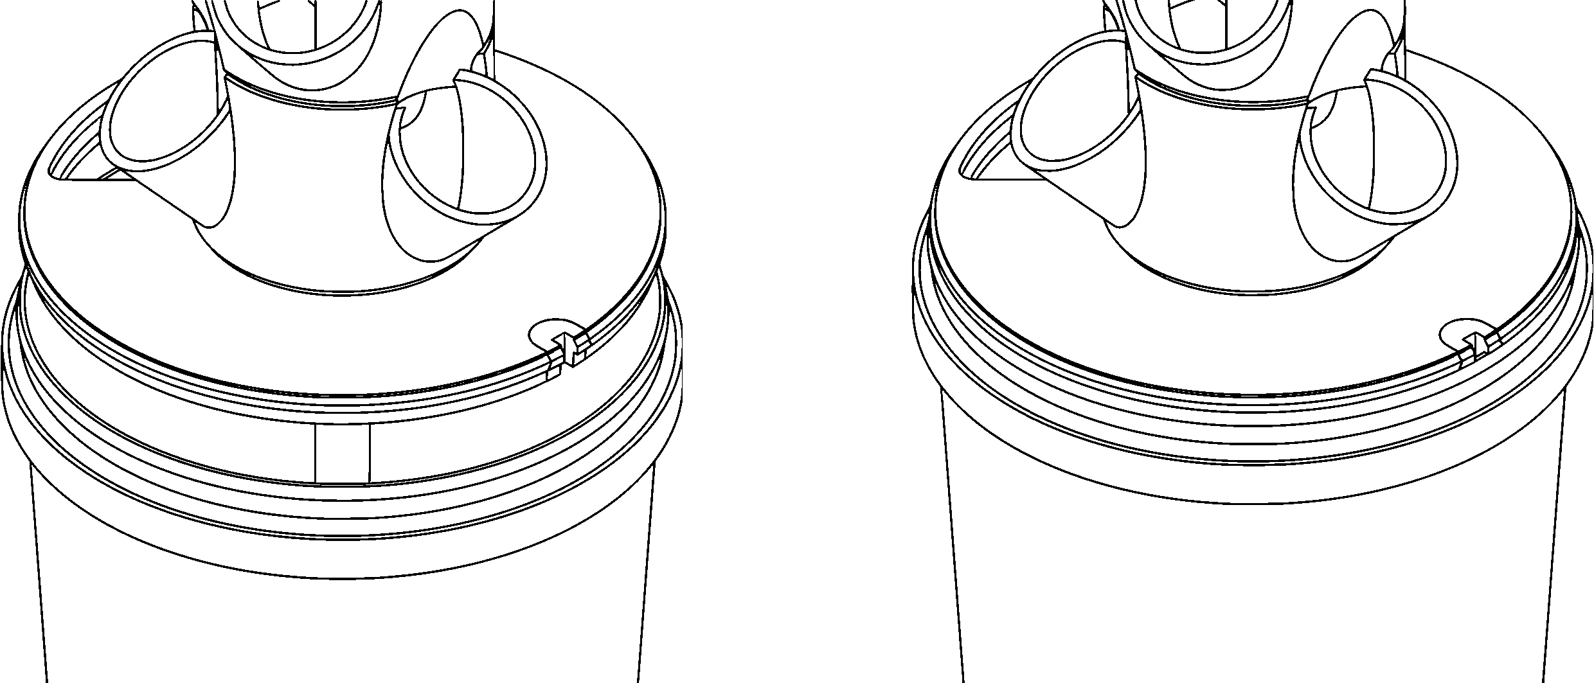
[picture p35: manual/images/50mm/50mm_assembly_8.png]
    
    \caption*{}
    \label{fig:50mm-eight}
\end{figure}

\begin{figure}[h]
    \centering
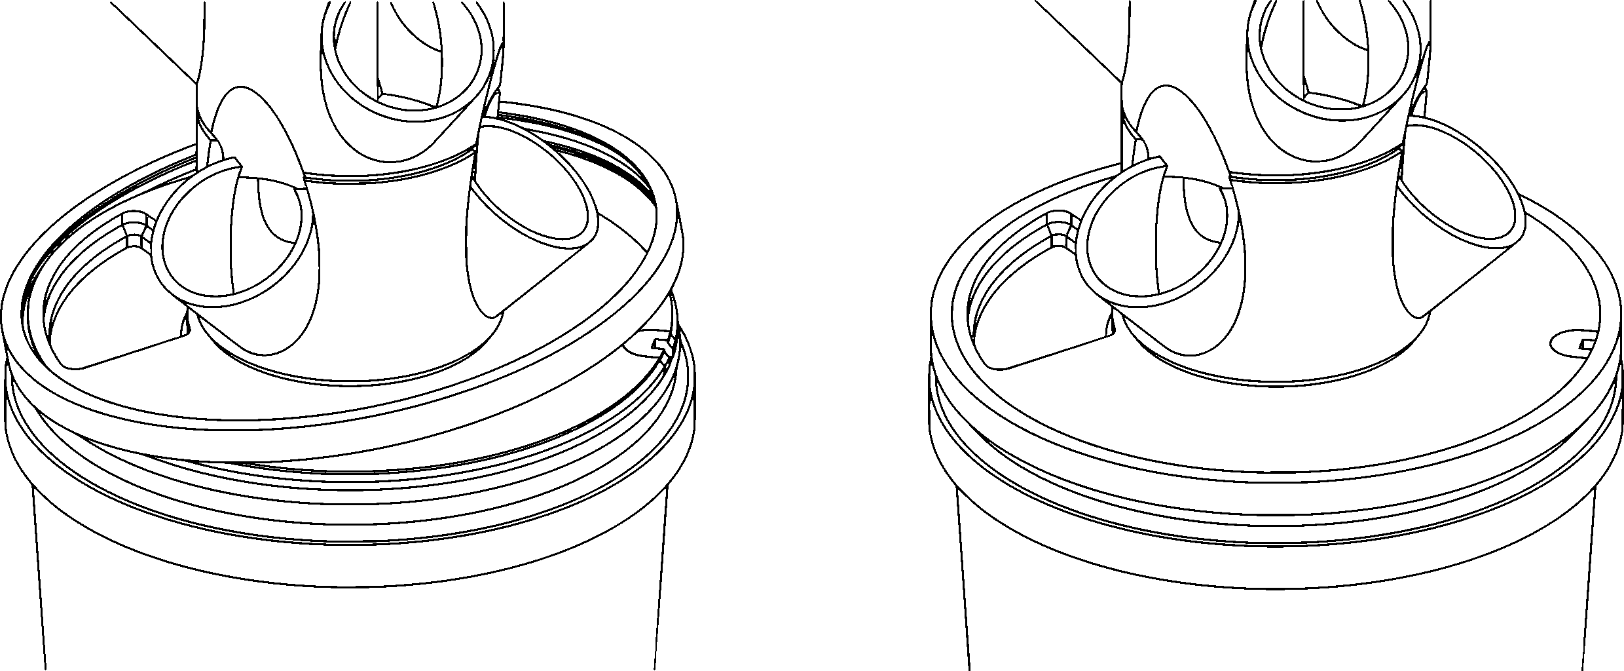
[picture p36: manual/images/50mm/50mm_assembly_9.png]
    
    \caption*{}
    \label{fig:50mm-nine}
\end{figure}
\begin{figure}[h]
    \centering
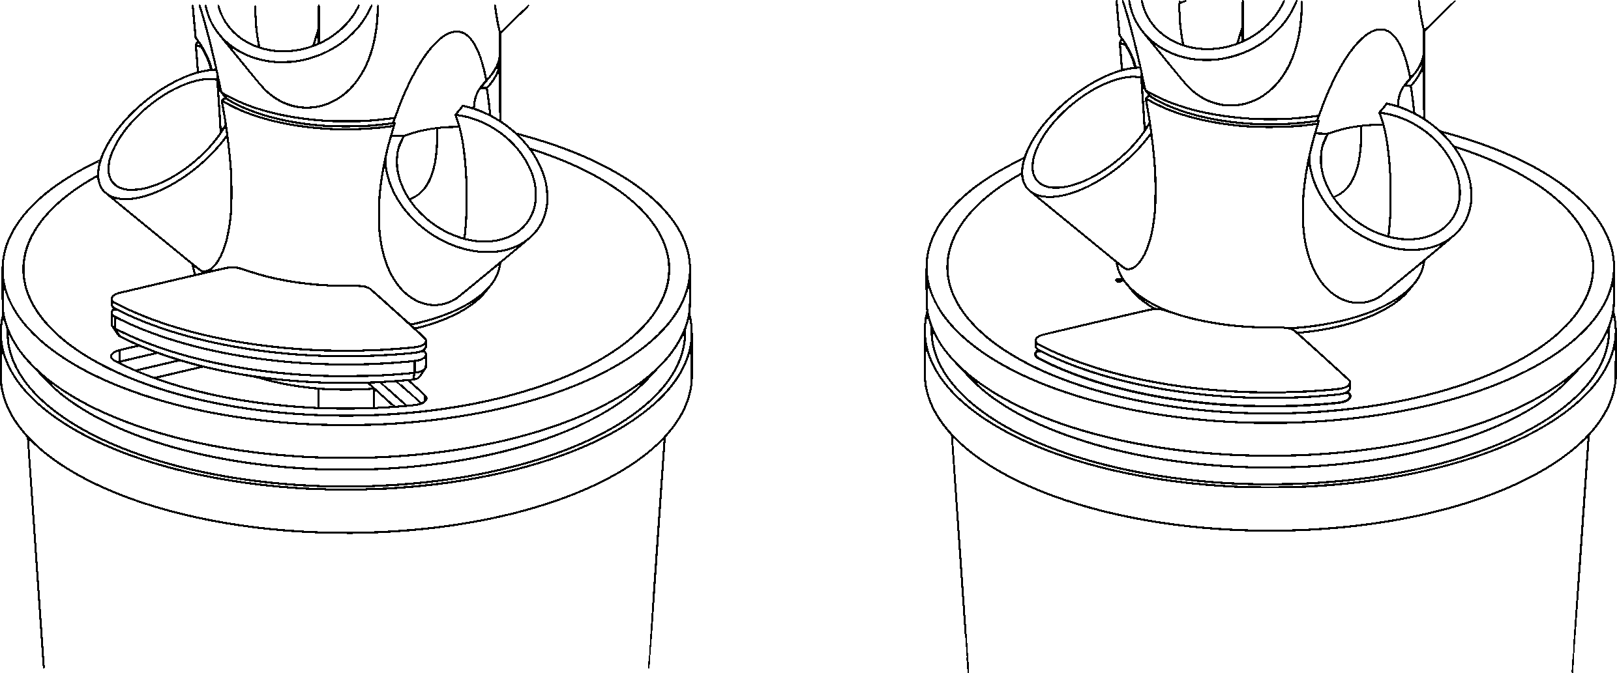
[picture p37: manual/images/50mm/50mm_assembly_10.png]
    
    \caption*{}
    \label{fig:50mm-ten}
\end{figure}
\begin{figure}[h!]
    \centering
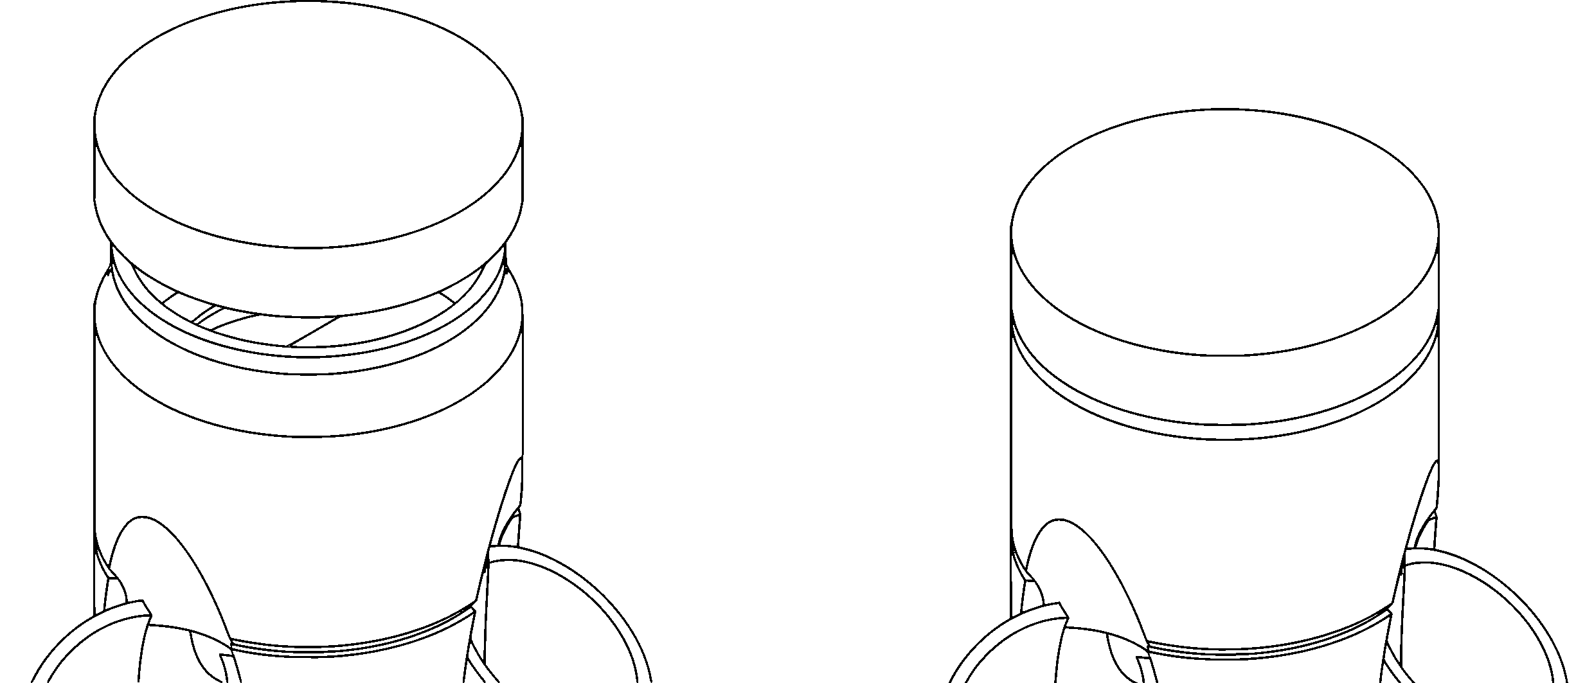
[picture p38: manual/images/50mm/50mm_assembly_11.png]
    
    \caption*{}
    \label{fig:50mm-eleven}
\end{figure}

\end{enumerate}

\setlength{\intextsep}{12.0pt plus 2.0pt minus 2.0pt}
\setlength{\floatsep}{12.0pt plus 2.0pt minus 2.0pt}
\setlength{\textfloatsep}{20.0pt plus 2.0pt minus 4.0pt}
\setlength{\belowcaptionskip}{0.0pt}

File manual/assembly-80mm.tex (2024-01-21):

\subsection{Parts}

\begin{center}
    \begin{minipage}{0.3\textwidth}
        \centering
        
        \captionof*{figure}{1x Bucket Lid}
    \end{minipage}
    \hfill
    \begin{minipage}{0.3\textwidth}
        \centering
        
        \captionof*{figure}{1x Bucket lid lock-ring}
    \end{minipage}
    \hfill
    \begin{minipage}{0.3\textwidth}
        \centering
        
        \captionof*{figure}{1x Bucket lid cap}
    \end{minipage}

    \vspace{8pt}
    \rule{\textwidth}{0.5pt}
    \vspace{2pt}

    \begin{minipage}{0.3\textwidth}
        \centering
        
        \captionof*{figure}{1x Two-wire cable gland}
    \end{minipage}
    \hfill
    \begin{minipage}{0.3\textwidth}
        \centering
        
        \captionof*{figure}{1x Three-wire cable gland}
    \end{minipage}
    \hfill
    \begin{minipage}{0.3\textwidth}
        \centering
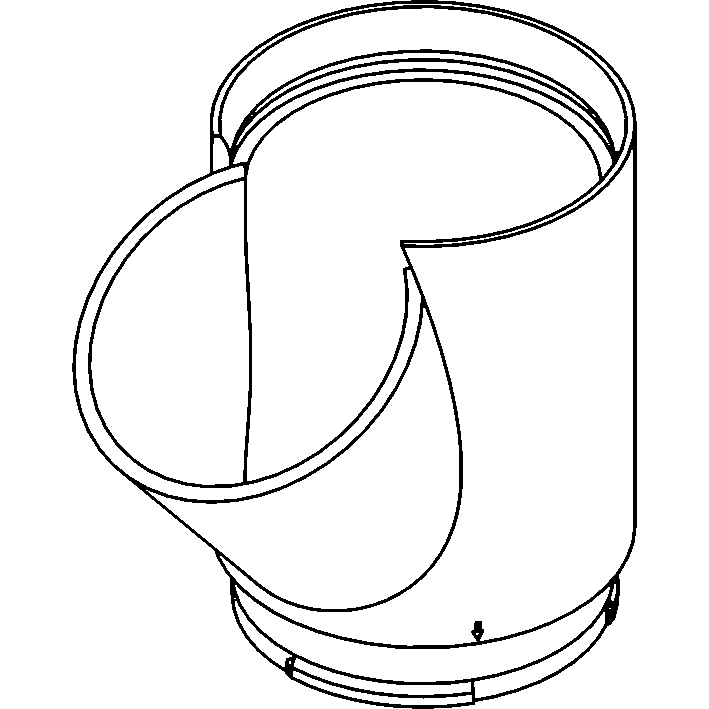
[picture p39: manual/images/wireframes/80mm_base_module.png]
        
        \captionof*{figure}{1x Twist-lock base module}
    \end{minipage}

    \vspace{8pt}
    \rule{\textwidth}{0.5pt}
    \vspace{2pt}

    \begin{minipage}{0.3\textwidth}
        \centering
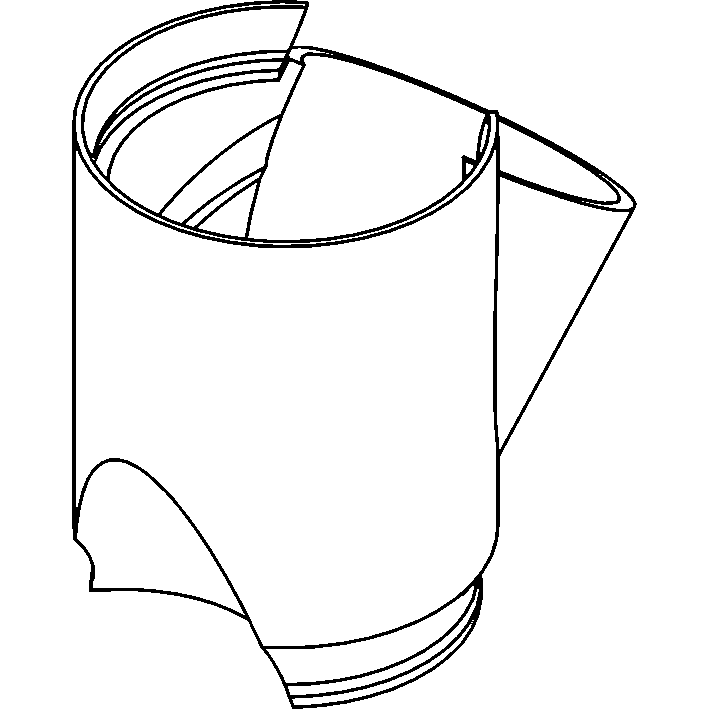
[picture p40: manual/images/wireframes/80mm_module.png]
        
        \captionof*{figure}{4x Snap-fit module}
    \end{minipage}
    \hfill
    \begin{minipage}{0.3\textwidth}
        \centering
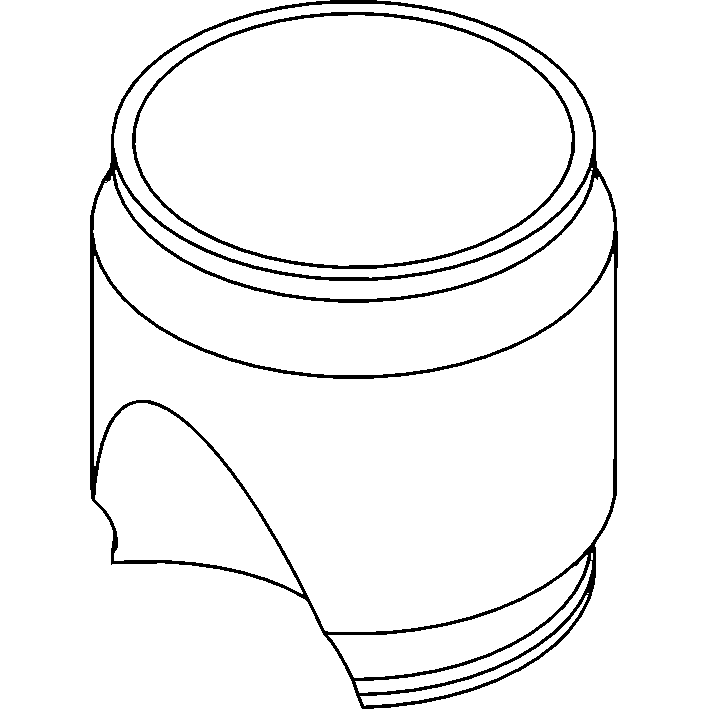
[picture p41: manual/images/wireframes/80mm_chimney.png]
        
        \captionof*{figure}{1x Chimney module}
    \end{minipage}
    \hfill
    \begin{minipage}{0.3\textwidth}
        \centering
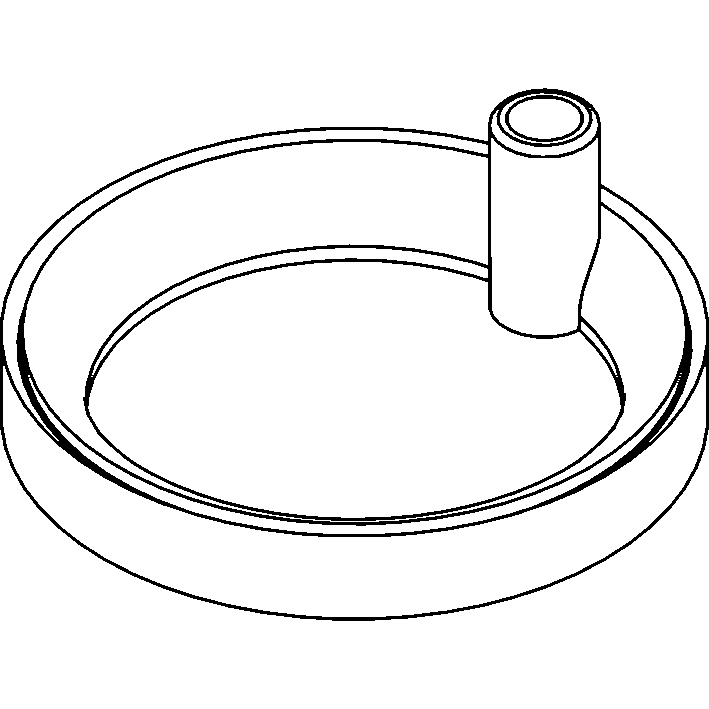
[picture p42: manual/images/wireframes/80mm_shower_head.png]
        
        \captionof*{figure}{1x Shower head}
    \end{minipage}

    % \vspace{8pt}
    % \rule{\textwidth}{0.5pt}
    % \vspace{2pt}

    \begin{minipage}{0.3\textwidth}
        \centering
        
        \captionof*{figure}{1x Chimney lid}
    \end{minipage}
    \hfill
    \begin{minipage}{0.3\textwidth}
        \centering
        
        \captionof*{figure}{1x 13mm hose adapter}
    \end{minipage}
    \hfill
    \begin{minipage}{0.3\textwidth}
        \centering
        
        \captionof*{figure}{1x 13mm Hose}
    \end{minipage}

    \vspace{8pt}
    \rule{\textwidth}{0.5pt}
    \vspace{2pt}

    \begin{minipage}{0.3\textwidth}
        \centering
        
        \captionof*{figure}{1x 5L Bucket}
    \end{minipage}
\end{center}

\clearpage

\setlength{\intextsep}{15.0pt plus 0.0pt minus 0.0pt}
\setlength{\floatsep}{0.0pt plus 0.0pt minus 0.0pt}
\setlength{\textfloatsep}{15.0pt plus 0.0pt minus 0.0pt}
\setlength{\belowcaptionskip}{-20.0pt}

\subsection{Assembly}

\begin{enumerate}

\item Align the arrow at the base of the \textbf{twist-lock base module} with the arrow on the top of the \textbf{bucket lid}. Carefully insert the base of the module into the hole in the center of the bucket lid when the arrows are aligned.

\item Once the \textbf{twist-lock base module} is inserted into the \textbf{bucket lid}, twist the module clockwise until you feel it stop. \textbf{Do not twist past this point.}

\begin{figure}[h]
    \centering
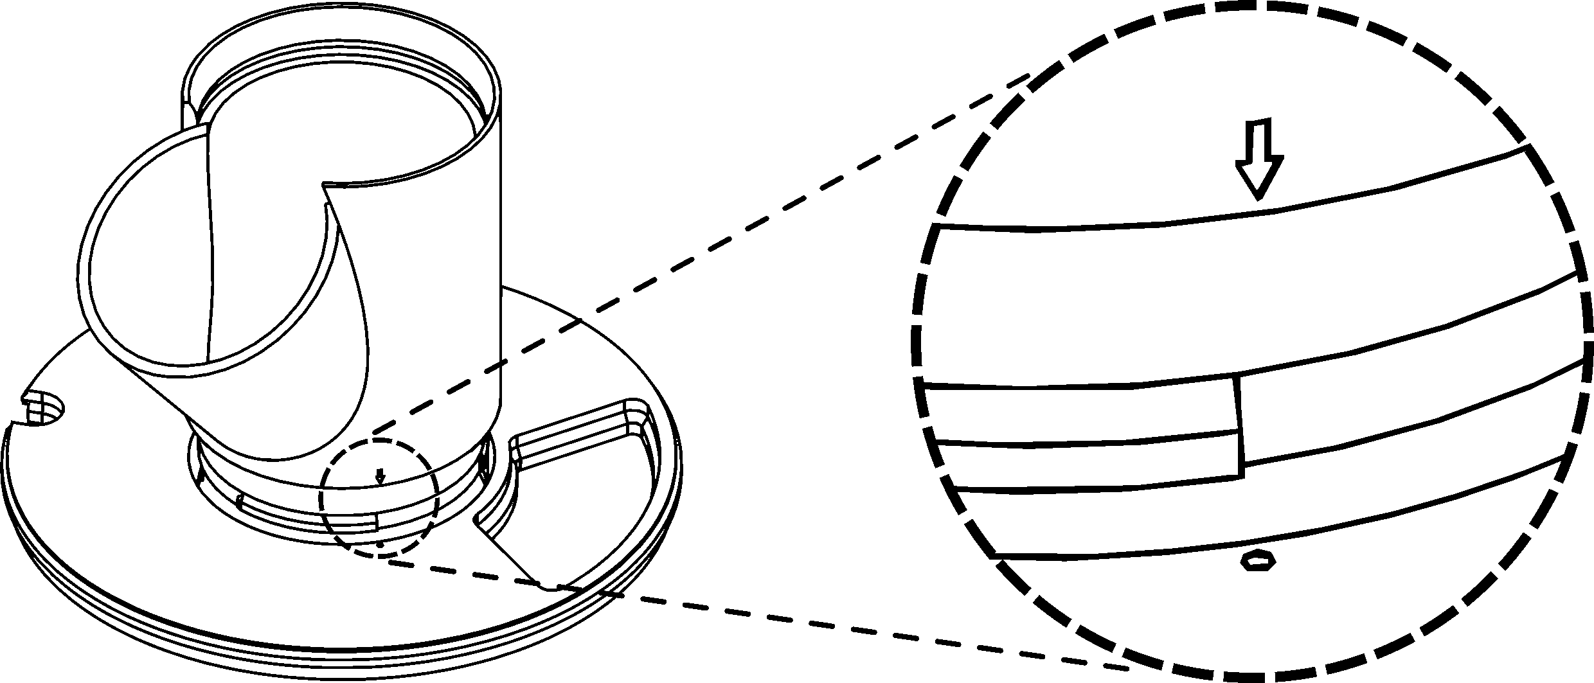
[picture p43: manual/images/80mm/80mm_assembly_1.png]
    
    \caption*{}
    \label{fig:80mm-one}
\end{figure}
\begin{figure}[h!]
    \centering
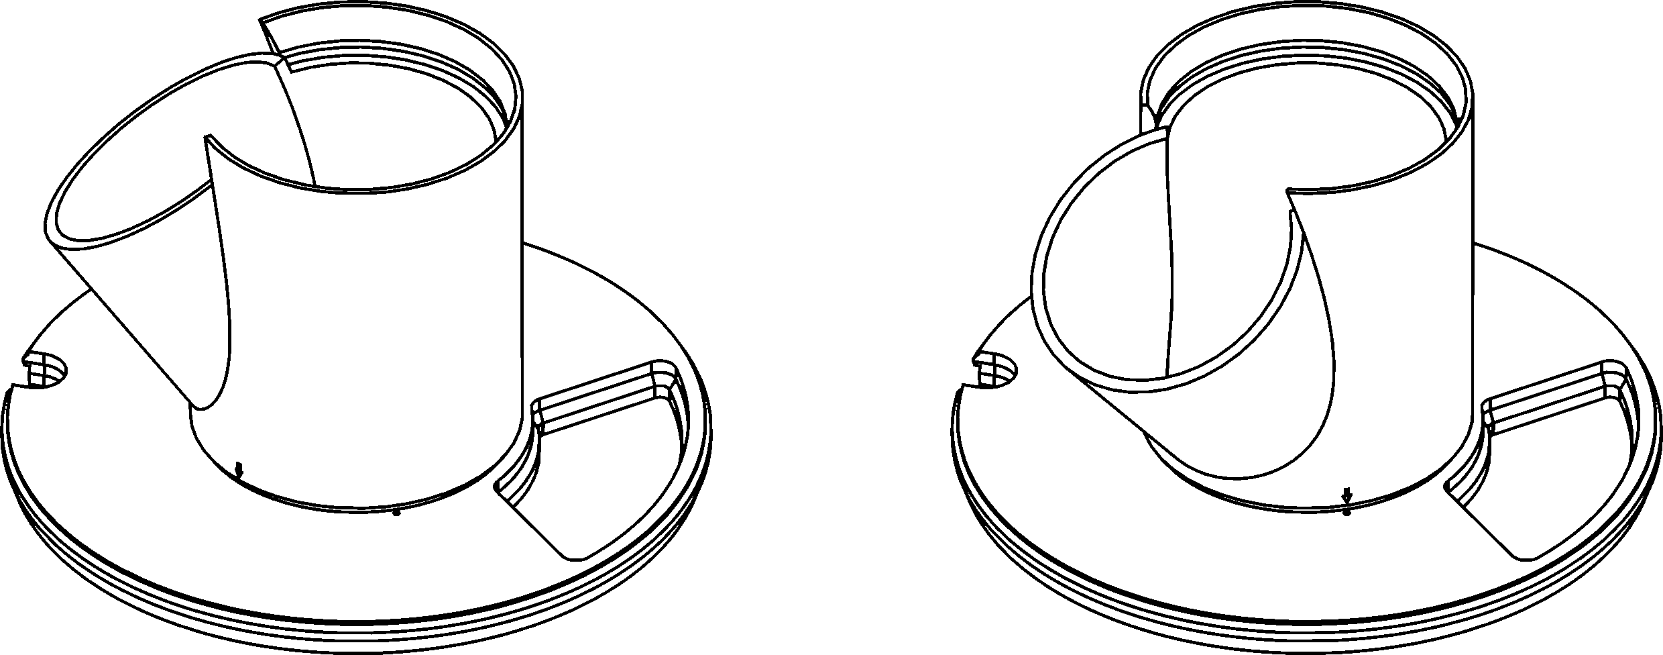
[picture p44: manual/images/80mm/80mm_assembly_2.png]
    
    \caption*{}
    \label{fig:80mm-two}
\end{figure}

\item Align the bottom of a \textbf{snap-fit module} with the top of the \textbf{twist-lock base module} so that the net pot receptacles of each module are facing 180 degrees away from one another.

\item With the pot receptacle of the lower module facing toward you, first push the \textbf{rear} of the upper module down into the snap-fit receiver of the lower module.

\item With the rear of the upper module seated in the snap-fit receiver of the lower module, carefully push down the \textbf{fore} of the upper module into the snap-fit receiver of the lower module. The foot of the upper module should seat fully into the snap-fit receiver of the lower module.

\begin{figure}[h]
    \centering
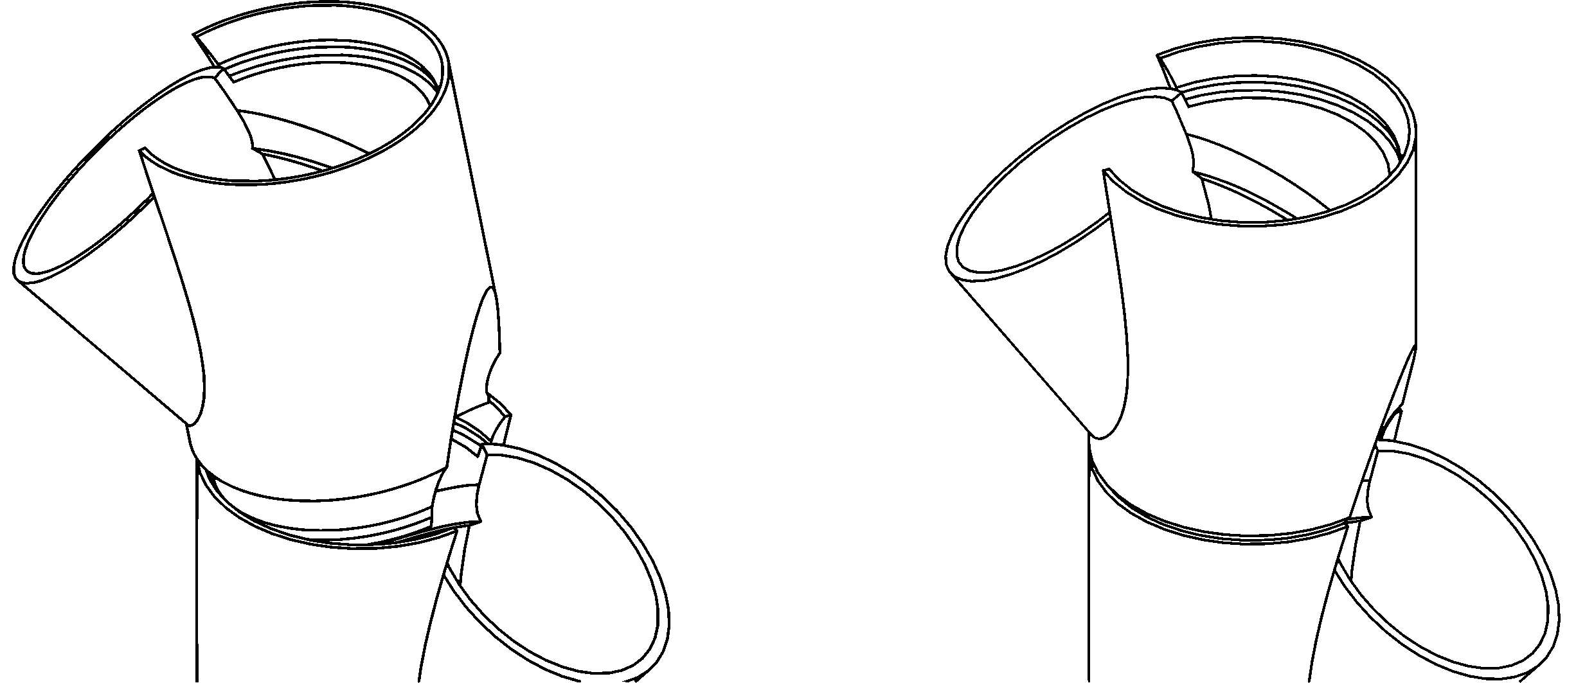
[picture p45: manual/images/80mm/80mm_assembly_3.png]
    
    \caption*{}
    \label{fig:80mm-three}
\end{figure}
\begin{figure}[h!]
    \centering
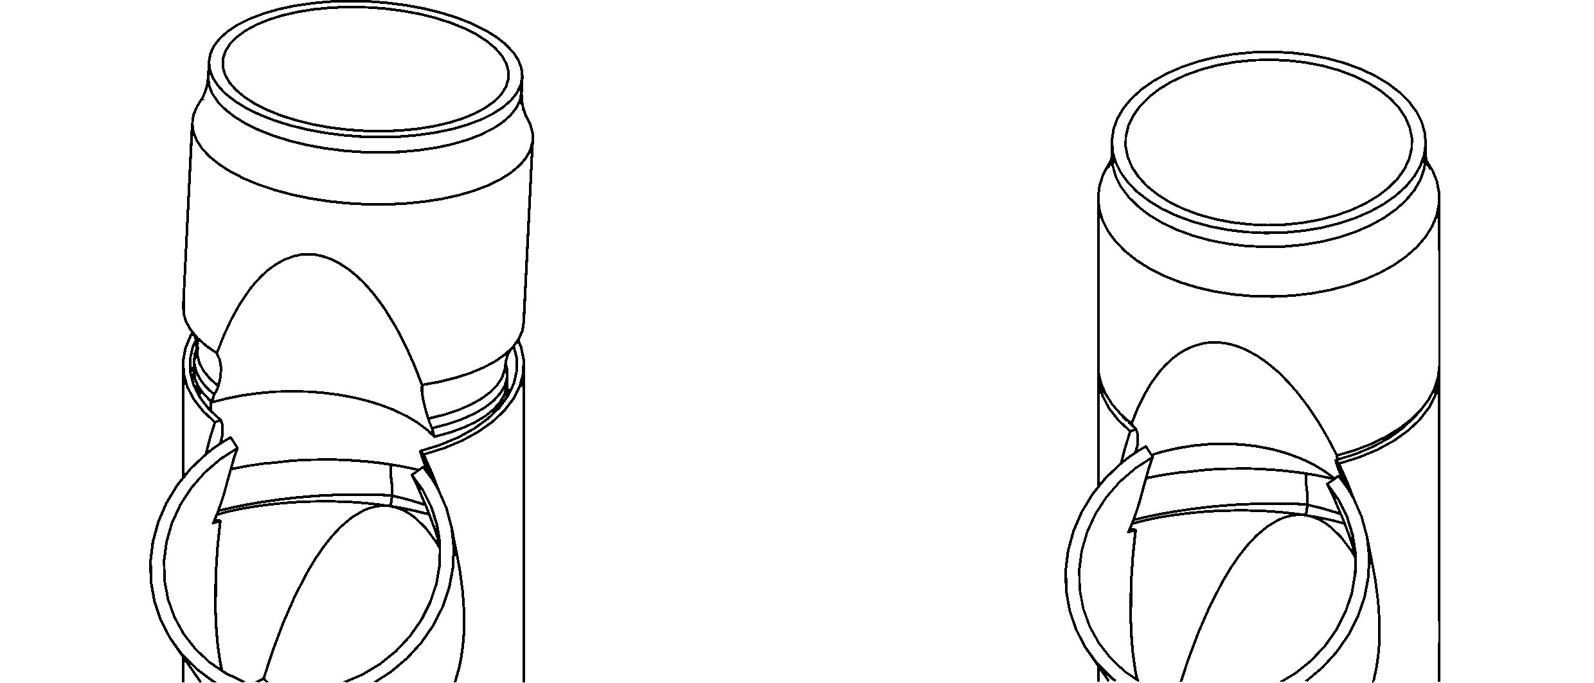
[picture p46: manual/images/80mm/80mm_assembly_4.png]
    
    \caption*{}
    \label{fig:80mm-four}
\end{figure}

\item Repeat steps 3 through 5 with the remaining planter modules.

\item Using the same method, insert the \textbf{chimney module} into the snap-fit receiver of the topmost planter module.

\item Insert the water inlet of the \textbf{shower head} into one end of the \textbf{13mm hose}.

\begin{figure}[h!]
    \centering
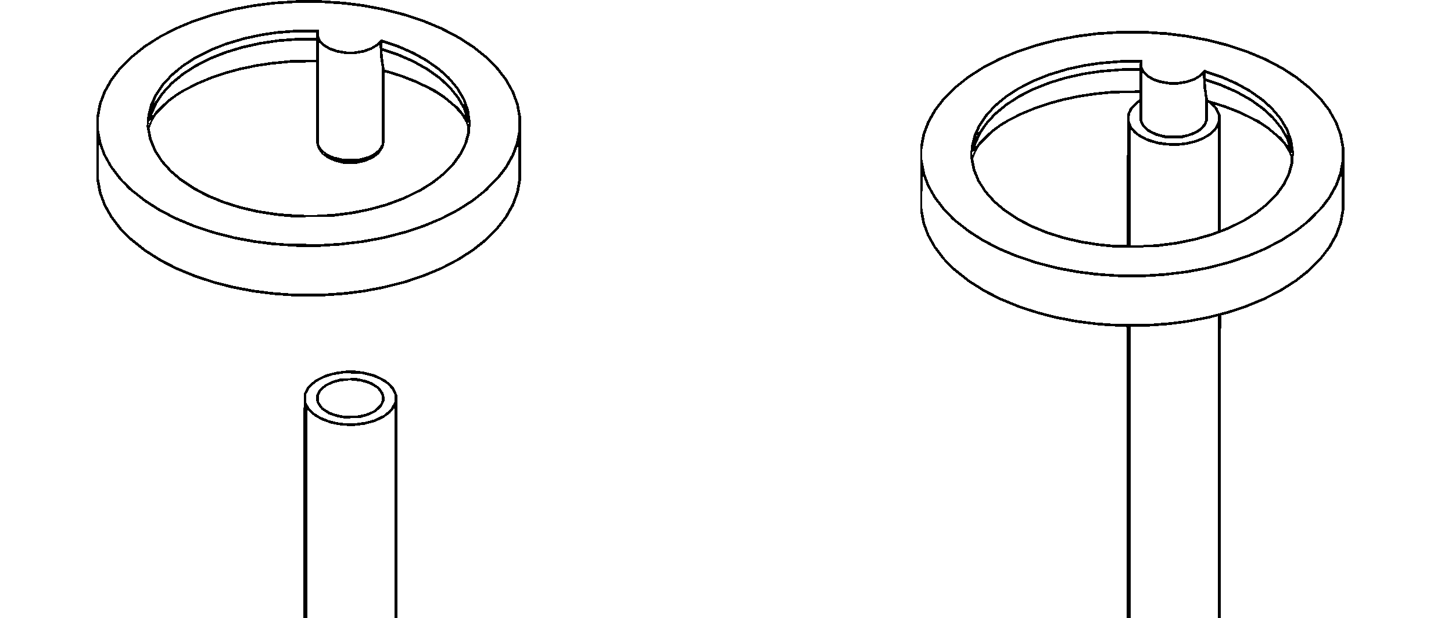
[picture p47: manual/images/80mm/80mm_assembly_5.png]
    
    \caption*{}
    \label{fig:80mm-five}
\end{figure}
\begin{figure}[h!]
    \centering
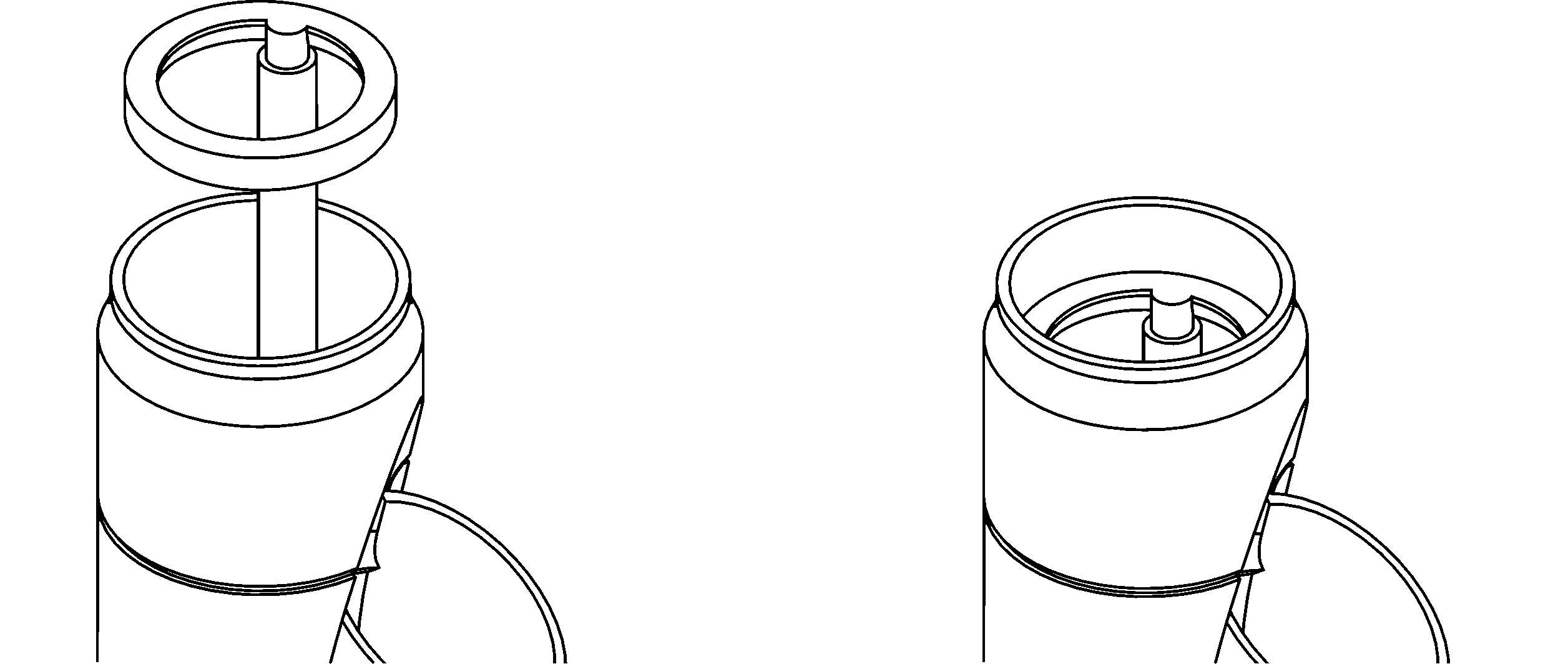
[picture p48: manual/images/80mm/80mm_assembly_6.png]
    
    \caption*{}
    \label{fig:80mm-six}
\end{figure}

\item Insert the opposite end of the \textbf{13mm hose} into the tower through the top of the \textbf{chimney module}, then insert the \textbf{shower head} into the top of the chimney module and push it down as far as it will go. Do not force the shower head further into the chimney module than it will go. The shower head is designed to fit snugly into the chimney module to aid the laminar flow of water over the inner wall of the tower, so \textbf{be careful not to angle the shower head as you insert it.}

\item If needed, twist the shower head so that the hose descends the tower adjacent to the net pot receptacles.

\item Insert the appropriate \textbf{bucket lid cable gland} for your chosen pump's power cord into the cable gland receiver of the \textbf{bucket lid}. Be careful to ensure that the cable gland is oriented correctly, or the bucket lid won't sit properly on the bucket.

\begin{figure}[h!]
    \centering
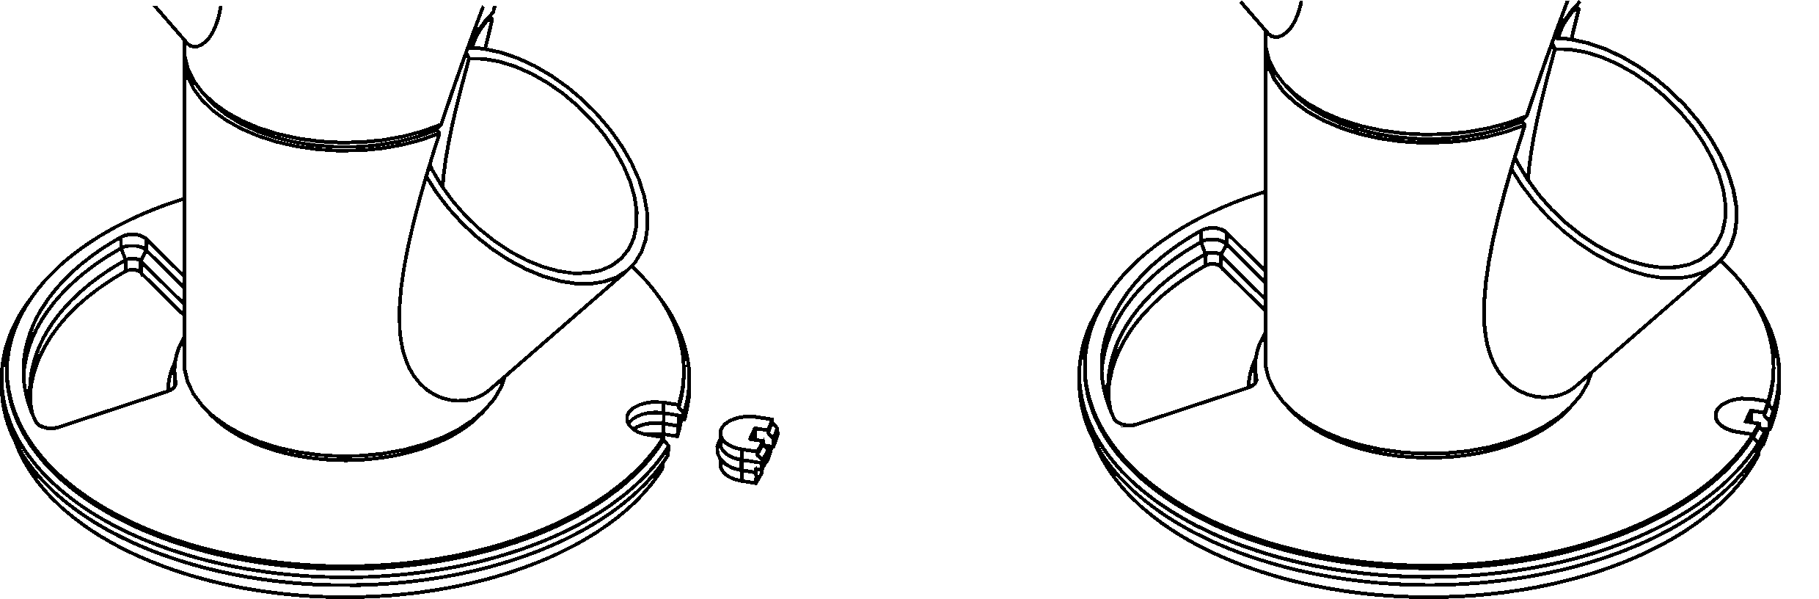
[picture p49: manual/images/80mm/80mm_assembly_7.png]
    
    \caption*{}
    \label{fig:80mm-seven}
\end{figure}

\item Place your \textbf{submersible pump} in the \textbf{5L bucket}.

\item If using an Aqua One 103 pump or other Aqua One pump with the same outlet, insert the 13mm end of the \textbf{13mm hose adapter} into the free end of the 13mm hose. If using a different pump, appropriate adapters will need to be provided by the user.

\item While holding the tower so that the bucket lid hovers just above the lip of the bucket, connect the free end of the 13mm hose to the outlet of the submersible pump. You may need to adjust the position of the pump in the bucket to ensure that the pump outlet aligns with the hose.

\item Lower the bucket lid onto the lip of the bucket, ensuring that the power cord of the pump is routed through the bucket lid cable gland. As the bucket lid is lowered, gently pull the shower head upward inside the chimney so that the hose is straightened but not taut.

\begin{figure}[h]
    \centering
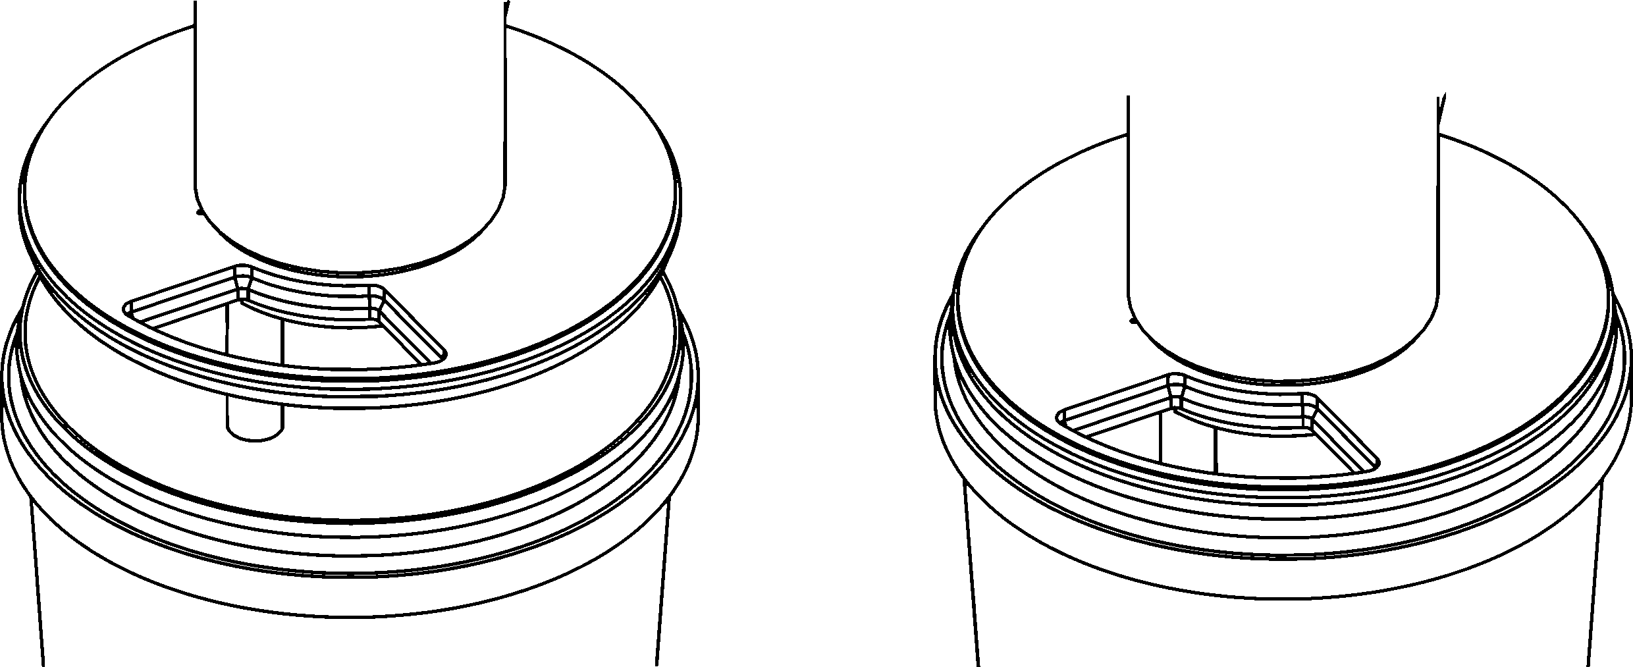
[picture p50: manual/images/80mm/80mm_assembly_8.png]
    
    \caption*{}
    \label{fig:80mm-eight}
\end{figure}

\item Lower the \textbf{bucket lid lock-ring}, with its flat side facing upward, down over the top of the tower. Align the lock-ring with the edge of the bucket lid, then carefully push the lock-ring down into place around the bucket-lid. It may be easiest to work from one point on the lock-ring and around to the other side in both directions simultaneously with both thumbs.

\item Insert the \textbf{bucket lid cap}, with its flat side facing upward, into the cap opening in the bucket lid.

\begin{figure}[h]
    \centering
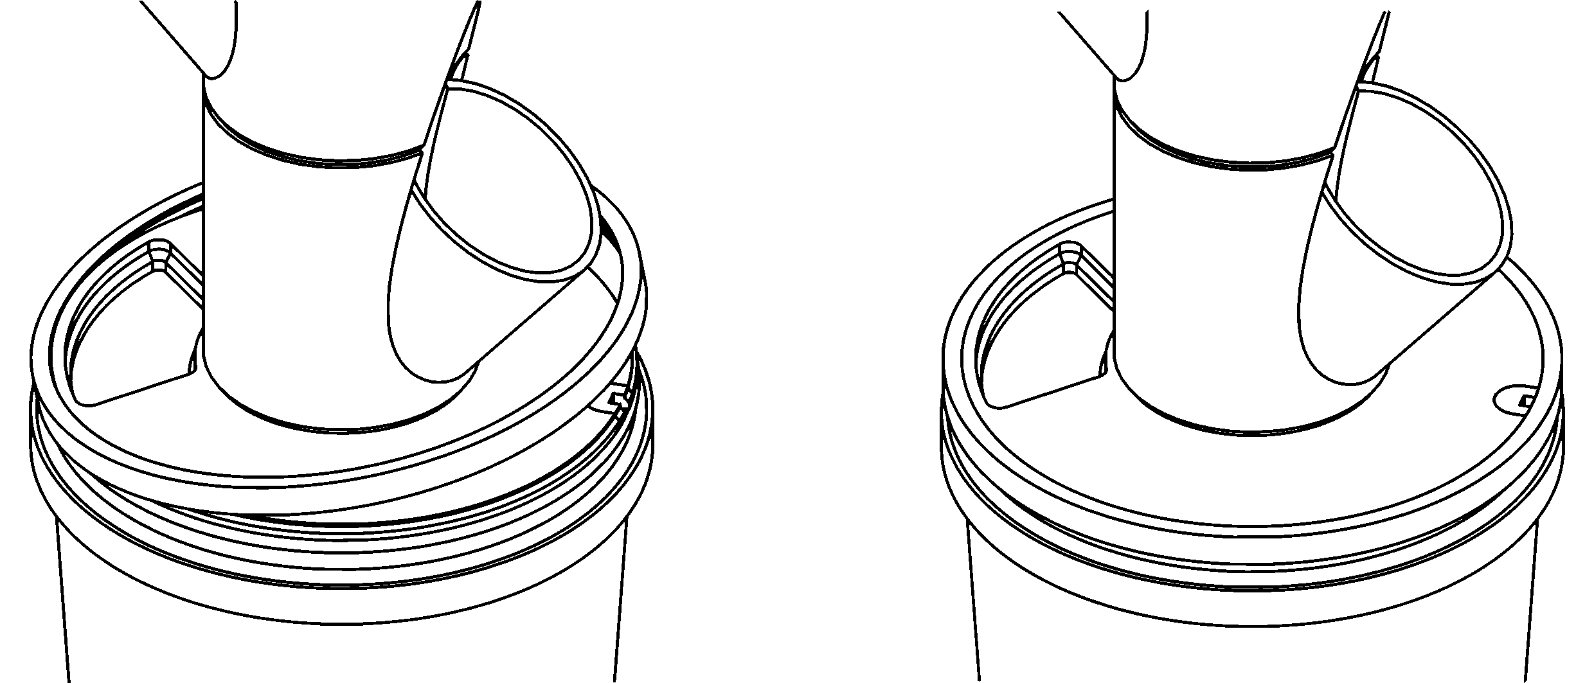
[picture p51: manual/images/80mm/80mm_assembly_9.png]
    
    \caption*{}
    \label{fig:80mm-nine}
\end{figure}

\item Place the \textbf{chimney lid}, with its flat side facing upward, on top of the tower chimney.

\begin{figure}[h]
    \centering
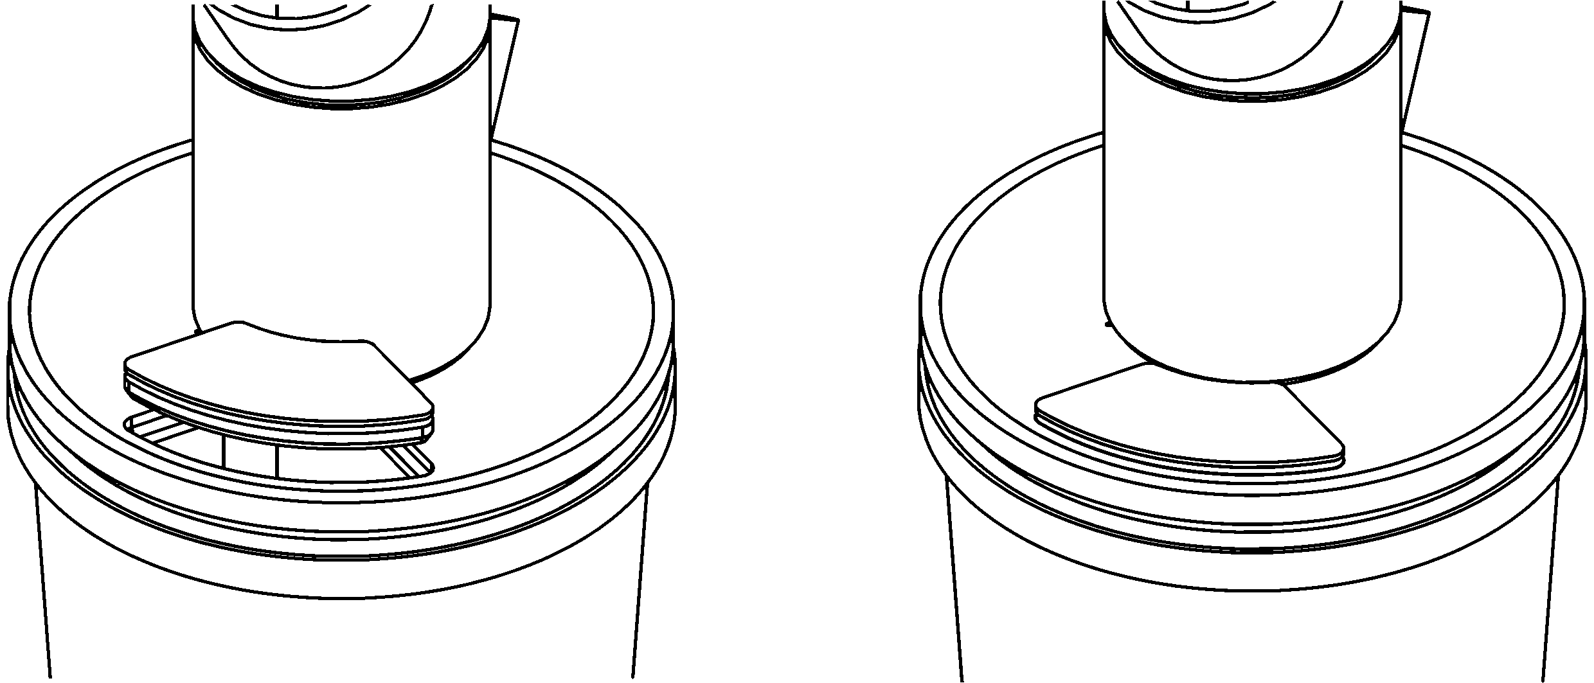
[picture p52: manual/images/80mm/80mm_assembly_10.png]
    
    \caption*{}
    \label{fig:80mm-ten}
\end{figure}
\begin{figure}[h]
    \centering
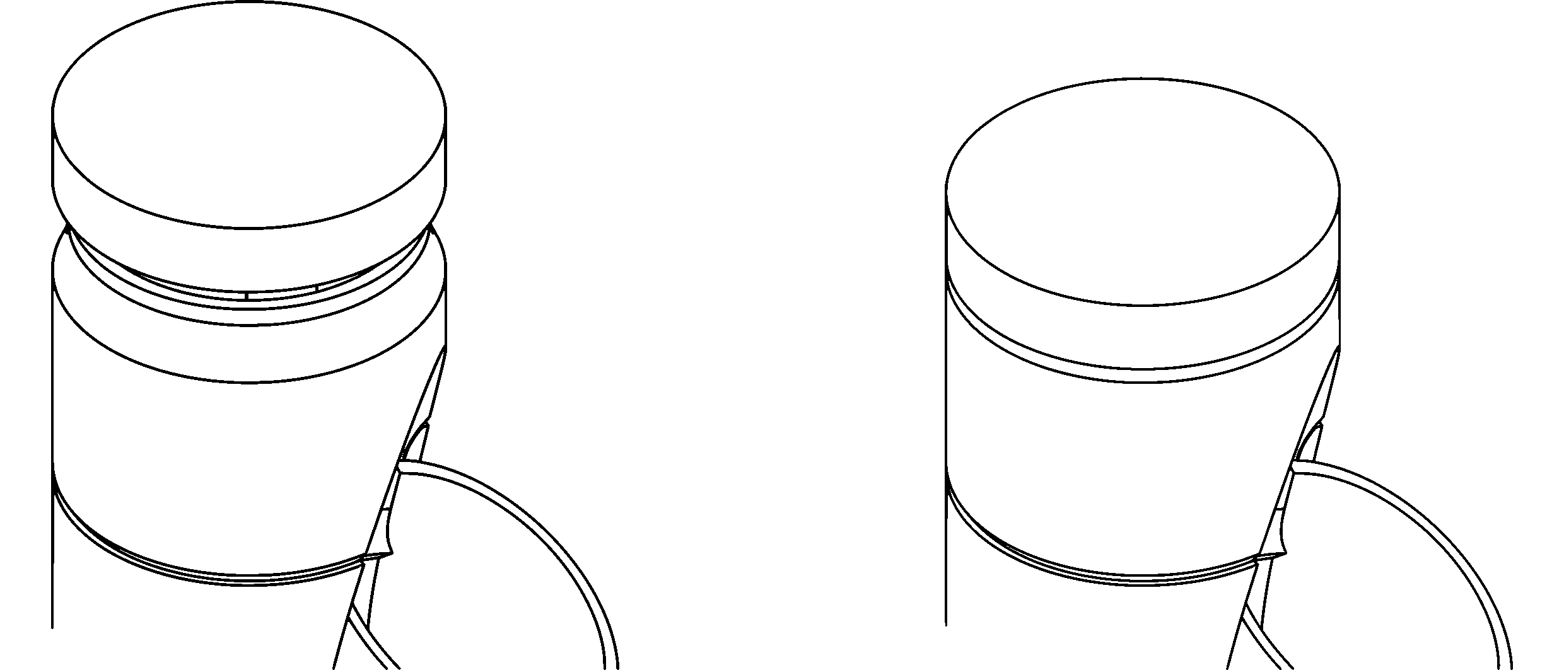
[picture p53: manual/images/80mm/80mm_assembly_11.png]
    
    \caption*{}
    \label{fig:80mm-eleven}
\end{figure}

\end{enumerate}

\setlength{\intextsep}{12.0pt plus 2.0pt minus 2.0pt}
\setlength{\floatsep}{12.0pt plus 2.0pt minus 2.0pt}
\setlength{\textfloatsep}{20.0pt plus 2.0pt minus 4.0pt}
\setlength{\belowcaptionskip}{0.0pt}

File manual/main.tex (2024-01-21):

%% Overleaf			
%% Software Manual and Technical Document Template	
%% 									
%% This provides an example of a software manual created in Overleaf.

\documentclass{tower-manual}

\usepackage{draftwatermark}

% Packages used in this example
\usepackage{graphicx}  % for including images
\graphicspath{ {./images} }
\usepackage{microtype} % for typographical enhancements
\usepackage[hidelinks]{hyperref}  % for hyperlinks
\usepackage[a5paper,top=2cm,bottom=2cm,left=1cm,right=1cm]{geometry} % for setting page size and margins
\usepackage{enumitem}
\setlist{itemsep=0.25mm}
\usepackage{lipsum}

\usepackage{caption}
% \DeclareCaptionLabelFormat{simple}
\DeclareCaptionLabelSeparator{none}{}
\captionsetup{labelformat=simple, labelsep=none}

% Custom macros used in this example document
\newcommand{\doclink}[2]{\href{#1}{#2}\footnote{\url{#1}}}
\newcommand{\cs}[1]{\texttt{\textbackslash #1}}

% Frontmatter data; appears on title page
\title{Dani's Indoor Grow Towers \\User Manual}
\author{Rev. 0.0.1}
\date{}
% \author{Overleaf}
% \softwarelogo{\includegraphics[width=8cm]{logo}}

\begin{document}

\pagenumbering{gobble}

\begin{titlepage}
    \maketitle

    \begin{center}
        \begin{minipage}{0.45\textwidth}
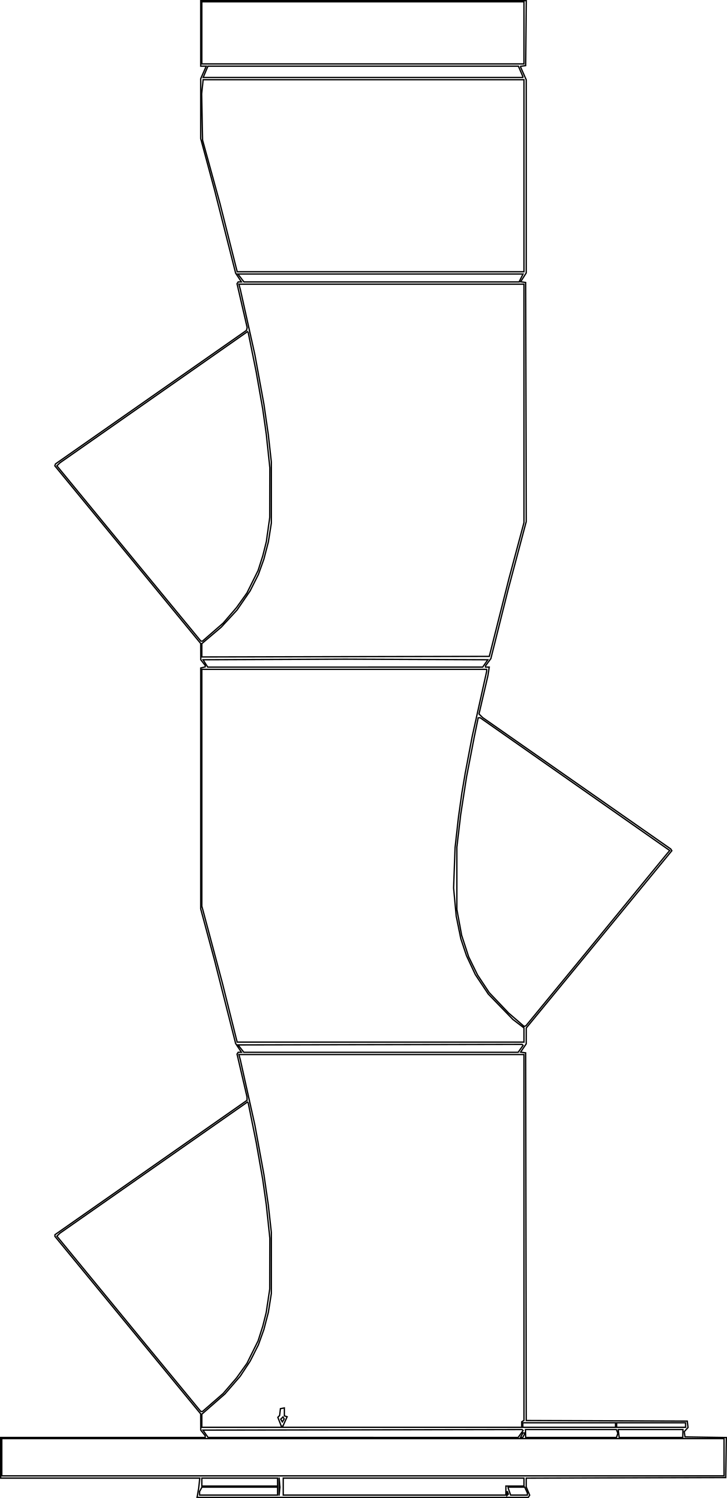
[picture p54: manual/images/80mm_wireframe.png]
            
        \end{minipage}
        \hfill
        \begin{minipage}{0.45\textwidth}
            
        \end{minipage}
    \end{center}
\end{titlepage}

\blankpage

\tableofcontents

\newpage
\blankpage

\pagenumbering{arabic}

\section{Introduction}

\lipsum[1-2]

\newpage

\section{Precautions}

\input{precautions}

\newpage

\section{Assembly Instructions -- 80mm}

\input{assembly-80mm}

\clearpage

\section{Assembly Instructions -- 50mm}

\input{assembly-50mm}

\clearpage

\section{Cleaning Suggestions}

\input{cleaning-suggestions}

\end{document}

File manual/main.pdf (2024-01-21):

# Dani’s Indoor Grow Towers User Manual


# DRAFT

### Rev. 0.0.1

# DRAFT

# DRAFT

## Contents

1 Introduction | 1
2 Precautions | 2
3 Assembly Instructions – 80mm | 3
4 Assembly Instructions – 50mm | 11
5 Cleaning Suggestions | 18

# DRAFT

# DRAFT

## 1 Introduction

Lorem ipsum dolor sit amet, consectetuer adipiscing elit. Ut purus elit, vestibulum ut, placerat ac, adipiscing vitae, felis. Curabitur dictum gravida mauris. Nam arcu libero, nonummy eget, consectetuer id, vulputate a, magna. Donec vehicula augue eu neque. Pellentesque habitant morbi tristique senectus et netus et malesuada fames ac turpis egestas. Mauris ut leo. Cras viverra metus rhoncus sem. Nulla et lectus vestibulum urna fringilla ultrices. Phasellus eu tellus sit amet tortor gravida placerat. Integer sapien est, iaculis in, pretium quis, viverra ac, nunc. Praesent eget sem vel leo ultrices bibendum. Aenean faucibus. Morbi dolor nulla, malesuada eu, pulvinar at, mollis ac, nulla. Curabitur auctor semper nulla. Donec varius orci eget risus. Duis nibh mi, congue eu, accumsan eleifend, sagittis quis, diam. Duis eget orci sit amet orci dignissim rutrum.
Nam dui ligula, fringilla a, euismod sodales, sollicitudin vel, wisi. Morbi auctor lorem non justo. Nam lacus libero, pretium at, lobortis vitae, ultricies et, tellus. Donec aliquet, tortor sed accumsan bibendum, erat ligula aliquet magna, vitae ornare odio metus a mi. Morbi ac orci et nisl hendrerit mollis. Suspendisse ut massa. Cras nec ante. Pellentesque a nulla. Cum sociis natoque penatibus et magnis dis parturient montes, nascetur ridiculus mus. Aliquam tincidunt urna. Nulla ullamcorper vestibulum turpis. Pellentesque cursus luctus mauris.

# DRAFT

## 2 Precautions

- Proper sanitation is paramount! Ensure your system is cleaned: before and after each growing cycle; if excessive growth of algae, fungus, or biofilm occurs; or if you notice any other signs of bacterial, fungal, algal, or other unwanted contamination. This is to minimize the risk of hazardous pathogens both to your plants and to you.
- Remember that your tower is a water vessel. To minimize risk in the event of a spill, place your tower well away from electrical devices, electrical outlets, and any other items which may be damaged by water or which may present a hazard in the presence of water.
- The components of your tower are not dishwasher-safe.
- Your tower is designed only to be placed indoors. Placing your tower outdoors may result in damage.

## 3 Assembly Instructions – 80mm

### 3.1 Parts

DRAFT; 1x Two-wire cable gland; 1x Three-wire cable gland; 1x Twist-lock base module

1x Bucket Lid | 1x Bucket lid lock-ring | 1x Bucket lid cap
4x Snap-fit module | 1x Chimney module | 1x Shower head

# DRAFT

1x Chimney lid | 1x 13mm hose adapter | 1x 13mm Hose

1x 5L Bucket

### 3.2 Assembly

1. Align the arrow at the base of the twist-lock base module with the arrow on the top of the bucket lid. Carefully insert the base of the module into the hole in the center of the bucket lid when the arrows are aligned.
2. Once the twist-lock base module is inserted into the bucket lid, twist

DRAFT; point.

the module clockwise until you feel it stop. Do not twist past this


3. Align the bottom of a snap-fit module with the top of the twist-lock base module so that the net pot receptacles of each module are facing 180 degrees away from one another.

# DRAFT

4. With the pot receptacle of the lower module facing toward you, first push the rear of the upper module down into the snap-fit receiver of the lower module.
5. With the rear of the upper module seated in the snap-fit receiver of the lower module, carefully push down the fore of the upper module into the snap-fit receiver of the lower module. The foot of the upper module should seat fully into the snap-fit receiver of the lower module.


6. Repeat steps 3 through 5 with the remaining planter modules.
7. Using the same method, insert the chimney module into the snap-fit receiver of the topmost planter module.

8. Insert the water inlet of the shower head into one end of the 13mm hose.

DRAFT

9. Insert the opposite end of the 13mm hose into the tower through the top of the chimney module, then insert the shower head into the top of the chimney module and push it down as far as it will go. Do not force the shower head further into the chimney module than it will go. The shower head is designed to fit snugly into the chimney module to aid the laminar flow of water over the inner wall of the tower, so be careful not to angle the shower head as you insert it.
10. If needed, twist the shower head so that the hose descends the tower adjacent to the net pot receptacles.


# DRAFT

11. Insert the appropriate bucket lid cable gland for your chosen pump’s power cord into the cable gland receiver of the bucket lid. Be careful to ensure that the cable gland is oriented correctly, or the bucket lid won’t sit properly on the bucket.
12. Place your submersible pump in the 5L bucket.
13. If using an Aqua One 103 pump or other Aqua One pump with the same outlet, insert the 13mm end of the 13mm hose adapter into the free end of the 13mm hose. If using a different pump, appropriate adapters will need to be provided by the user.
14. While holding the tower so that the bucket lid hovers just above the lip of the bucket, connect the free end of the 13mm hose to the outlet of the submersible pump. You may need to adjust the position of the pump in the bucket to ensure that the pump outlet aligns with the hose.
15. Lower the bucket lid onto the lip of the bucket, ensuring that the power cord of the pump is routed through the bucket lid cable gland. As the bucket lid is lowered, gently pull the shower head upward inside the chimney so that the hose is straightened but not taut.
16. Lower the bucket lid lock-ring, with its flat side facing upward, down over the top of the tower. Align the lock-ring with the edge of the bucket lid, then carefully push the lock-ring down into place around the bucket-lid. It may be easiest to work from one point on the lock-ring and around to the other side in both directions simultaneously with both thumbs.

DRAFT; opening in the bucket lid.; tower chimney.

17. Insert the bucket lid cap, with its flat side facing upward, into the cap
18. Place the chimney lid, with its flat side facing upward, on top of the


# DRAFT


## 4 Assembly Instructions – 50mm

### 4.1 Parts

DRAFT; 1x Two-wire cable gland; 1x Three-wire cable gland; 1x Twist-lock base module

1x Bucket Lid | 1x Bucket lid lock-ring | 1x Bucket lid cap
5x Snap-fit module | 1x Chimney module | 1x Shower head

# DRAFT

1x Chimney lid | 1x 13mm hose adapter | 1x 13mm Hose

1x 5L Bucket

### 4.2 Assembly

1. Align the arrow at the base of the twist-lock base module with the arrow on the top of the bucket lid. Carefully insert the base of the module into the hole in the center of the bucket lid when the arrows are aligned.
2. Once the twist-lock base module is inserted into the bucket lid, twist

DRAFT; point.

the module clockwise until you feel it stop. Do not twist past this


3. Align the bottom of a snap-fit module with the top of the twist-lock base module so that the foot of the upper module fits into the receiver of the lower module, then gently push the upper module down until it snaps snugly together with the lower module.
4. Repeat step 3 with the remaining planter modules.


# DRAFT

5. Using the same method, insert the chimney module into the snap-fit receiver of the topmost planter module.
6. Insert the water inlet of the shower head into one end of the 13mm hose.
7. Insert the opposite end of the 13mm hose into the tower through the


# DRAFT

top of the chimney module, then insert the shower head into the top of the chimney module and push it down as far as it will go. Do not force the shower head further into the chimney module than it will go. The shower head is designed to fit snugly into the chimney module to aid the laminar flow of water over the inner wall of the tower, so be careful not to angle the shower head as you insert it.

8. Insert the appropriate bucket lid cable gland for your chosen pump’s power cord into the cable gland receiver of the bucket lid. Be careful to ensure that the cable gland is oriented correctly, or the bucket lid won’t sit properly on the bucket.


9. Place your submersible pump in the 5L bucket.
10. If using an Aqua One 103 pump or other Aqua One pump with the same outlet, insert the 13mm end of the 13mm hose adapter into the free end of the 13mm hose. If using a different pump, appropriate

# DRAFT

adapters will need to be provided by the user.

11. While holding the tower so that the bucket lid hovers just above the lip of the bucket, connect the free end of the 13mm hose to the outlet of the submersible pump. You may need to adjust the position of the pump in the bucket to ensure that the pump outlet aligns with the hose.
12. Lower the bucket lid onto the lip of the bucket, ensuring that the power cord of the pump is routed through the bucket lid cable gland. As the bucket lid is lowered, gently pull the shower head upward inside the chimney so that the hose is straightened but not taut.
13. Lower the bucket lid lock-ring, with its flat side facing upward, down over the top of the tower. Align the lock-ring with the edge of the bucket lid, then carefully push the lock-ring down into place around the bucket-lid. It may be easiest to work from one point on the lock-ring and around to the other side in both directions simultaneously with both thumbs.
14. Insert the bucket lid cap, with its flat side facing upward, into the cap opening in the bucket lid.
15. Place the chimney lid, with its flat side facing upward, on top of the tower chimney.


# DRAFT

# DRAFT

## 5 Cleaning Suggestions

Lorem ipsum dolor sit amet, consectetuer adipiscing elit. Ut purus elit, vestibulum ut, placerat ac, adipiscing vitae, felis. Curabitur dictum gravida mauris. Nam arcu libero, nonummy eget, consectetuer id, vulputate a, magna. Donec vehicula augue eu neque. Pellentesque habitant morbi tristique senectus et netus et malesuada fames ac turpis egestas. Mauris ut leo. Cras viverra metus rhoncus sem. Nulla et lectus vestibulum urna fringilla ultrices. Phasellus eu tellus sit amet tortor gravida placerat. Integer sapien est, iaculis in, pretium quis, viverra ac, nunc. Praesent eget sem vel leo ultrices bibendum. Aenean faucibus. Morbi dolor nulla, malesuada eu, pulvinar at, mollis ac, nulla. Curabitur auctor semper nulla. Donec varius orci eget risus. Duis nibh mi, congue eu, accumsan eleifend, sagittis quis, diam. Duis eget orci sit amet orci dignissim rutrum.
Nam dui ligula, fringilla a, euismod sodales, sollicitudin vel, wisi. Morbi auctor lorem non justo. Nam lacus libero, pretium at, lobortis vitae, ultricies et, tellus. Donec aliquet, tortor sed accumsan bibendum, erat ligula aliquet magna, vitae ornare odio metus a mi. Morbi ac orci et nisl hendrerit mollis. Suspendisse ut massa. Cras nec ante. Pellentesque a nulla. Cum sociis natoque penatibus et magnis dis parturient montes, nascetur ridiculus mus. Aliquam tincidunt urna. Nulla ullamcorper vestibulum turpis. Pellentesque cursus luctus mauris.
Nulla malesuada porttitor diam. Donec felis erat, congue non, volutpat at, tincidunt tristique, libero. Vivamus viverra fermentum felis. Donec nonummy pellentesque ante. Phasellus adipiscing semper elit. Proin fermentum massa ac quam. Sed diam turpis, molestie vitae, placerat a, molestie nec, leo. Maecenas lacinia. Nam ipsum ligula, eleifend at, accumsan nec, suscipit a, ipsum. Morbi blandit ligula feugiat magna. Nunc eleifend consequat lorem. Sed lacinia nulla vitae enim. Pellentesque tincidunt purus vel magna. Integer non enim. Praesent euismod nunc eu purus. Donec bibendum quam in tellus. Nullam cursus pulvinar lectus. Donec et mi. Nam vulputate metus eu enim. Vestibulum pellentesque felis eu massa.

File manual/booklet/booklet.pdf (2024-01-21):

# Dani’s Indoor Grow Towers


# DRAFT

# User Manual

### Rev. 0.0.1


# DRAFT

dignissim rutrum.

congue eu, accumsan eleifend, sagittis quis, diam. Duis eget orci sit amet orci

Curabitur auctor semper nulla. Donec varius orci eget risus. Duis nibh mi,

faucibus. Morbi dolor nulla, malesuada eu, pulvinar at, mollis ac, nulla.

quis, viverra ac, nunc. Praesent eget sem vel leo ultrices bibendum. Aenean

tellus sit amet tortor gravida placerat. Integer sapien est, iaculis in, pretium

rhoncus sem. Nulla et lectus vestibulum urna fringilla ultrices. Phasellus eu

netus et malesuada fames ac turpis egestas. Mauris ut leo. Cras viverra metus

vehicula augue eu neque. Pellentesque habitant morbi tristique senectus et
Nam arcu libero, nonummy eget, consectetuer id, vulputate a, magna. Donec

bulum ut, placerat ac, adipiscing vitae, felis. Curabitur dictum gravida mauris.
Lorem ipsum dolor sit amet, consectetuer adipiscing elit. Ut purus elit, vesti-

## 5 Cleaning Suggestions

Nam dui ligula, fringilla a, euismod sodales, sollicitudin vel, wisi. Morbi

cursus luctus mauris.

Aliquam tincidunt urna. Nulla ullamcorper vestibulum turpis. Pellentesque
natoque penatibus et magnis dis parturient montes, nascetur ridiculus mus.

Suspendisse ut massa. Cras nec ante. Pellentesque a nulla. Cum sociis

magna, vitae ornare odio metus a mi. Morbi ac orci et nisl hendrerit mollis.

et, tellus. Donec aliquet, tortor sed accumsan bibendum, erat ligula aliquet

auctor lorem non justo. Nam lacus libero, pretium at, lobortis vitae, ultricies Nulla malesuada porttitor diam. Donec felis erat, congue non, volutpat at,

Vestibulum pellentesque felis eu massa.
Nullam cursus pulvinar lectus. Donec et mi. Nam vulputate metus eu enim.
non enim. Praesent euismod nunc eu purus. Donec bibendum quam in tellus.

Sed lacinia nulla vitae enim. Pellentesque tincidunt purus vel magna. Integer

ipsum. Morbi blandit ligula feugiat magna. Nunc eleifend consequat lorem.

Maecenas lacinia. Nam ipsum ligula, eleifend at, accumsan nec, suscipit a,

ac quam. Sed diam turpis, molestie vitae, placerat a, molestie nec, leo.

pellentesque ante. Phasellus adipiscing semper elit. Proin fermentum massa

tincidunt tristique, libero. Vivamus viverra fermentum felis. Donec nonummy

19

# DRAFT

# DRAFT


18

# DRAFT

## Contents

### 1 Introduction 1

### 2 Precautions 2

### 3 Assembly Instructions – 80mm 3

### 4 Assembly Instructions – 50mm 11

### 5 Cleaning Suggestions 19

DRAFT opening in the bucket lid.; tower chimney.

14. Insert the bucket lid cap, with its flat side facing upward, into the cap
15. Place the chimney lid, with its flat side facing upward, on top of the


17

# DRAFT

# DRAFT


won’t sit properly on the bucket.

9. Place your submersible pump in the 5L bucket.
10. If using an Aqua One 103 pump or other Aqua One pump with the
same outlet, insert the 13mm end of the 13mm hose adapter into the

free end of the 13mm hose. If using a different pump, appropriate

adapters will need to be provided by the user.

11. While holding the tower so that the bucket lid hovers just above the

lip of the bucket, connect the free end of the 13mm hose to the outlet
of the submersible pump. You may need to adjust the position of the

pump in the bucket to ensure that the pump outlet aligns with the hose.
12. Lower the bucket lid onto the lip of the bucket, ensuring that the power
cord of the pump is routed through the bucket lid cable gland. As the

bucket lid is lowered, gently pull the shower head upward inside the

chimney so that the hose is straightened but not taut.

13. Lower the bucket lid lock-ring, with its flat side facing upward, down
over the top of the tower. Align the lock-ring with the edge of the
bucket lid, then carefully push the lock-ring down into place around the
bucket-lid. It may be easiest to work from one point on the lock-ring

and around to the other side in both directions simultaneously with

both thumbs.

16

# DRAFT

## 1 Introduction

Lorem ipsum dolor sit amet, consectetuer adipiscing elit. Ut purus elit, vesti-

bulum ut, placerat ac, adipiscing vitae, felis. Curabitur dictum gravida mauris.
Nam arcu libero, nonummy eget, consectetuer id, vulputate a, magna. Donec

vehicula augue eu neque. Pellentesque habitant morbi tristique senectus et
netus et malesuada fames ac turpis egestas. Mauris ut leo. Cras viverra metus

rhoncus sem. Nulla et lectus vestibulum urna fringilla ultrices. Phasellus eu

tellus sit amet tortor gravida placerat. Integer sapien est, iaculis in, pretium
quis, viverra ac, nunc. Praesent eget sem vel leo ultrices bibendum. Aenean

faucibus. Morbi dolor nulla, malesuada eu, pulvinar at, mollis ac, nulla.
Curabitur auctor semper nulla. Donec varius orci eget risus. Duis nibh mi,
congue eu, accumsan eleifend, sagittis quis, diam. Duis eget orci sit amet orci

dignissim rutrum.

Nam dui ligula, fringilla a, euismod sodales, sollicitudin vel, wisi. Morbi
auctor lorem non justo. Nam lacus libero, pretium at, lobortis vitae, ultricies

et, tellus. Donec aliquet, tortor sed accumsan bibendum, erat ligula aliquet

magna, vitae ornare odio metus a mi. Morbi ac orci et nisl hendrerit mollis.
Suspendisse ut massa. Cras nec ante. Pellentesque a nulla. Cum sociis

natoque penatibus et magnis dis parturient montes, nascetur ridiculus mus.
Aliquam tincidunt urna. Nulla ullamcorper vestibulum turpis. Pellentesque

cursus luctus mauris.

1

DRAFT

7. Insert the opposite end of the 13mm hose into the tower through the top of the chimney module, then insert the shower head into the top


aid the laminar flow of water over the inner wall of the tower, so

The shower head is designed to fit snugly into the chimney module to
force the shower head further into the chimney module than it will go.

of the chimney module and push it down as far as it will go. Do not

be

careful not to angle the shower head as you insert it.

8. Insert the appropriate bucket lid cable gland for your chosen pump’s
power cord into the cable gland receiver of the bucket lid. Be careful

to ensure that the cable gland is oriented correctly, or the bucket lid

15

# DRAFT

## 2 Precautions

•
hazardous pathogens both to your plants

algal, or other unwanted contamination. This is to minimize the risk of

biofilm occurs; or if you notice any other signs of bacterial, fungal,
and after each growing cycle; if excessive growth of algae, fungus, or

Proper sanitation is paramount! Ensure your system is cleaned: before

and to you.

•
or which may present a hazard in the presence of water.

electrical outlets, and any other items which may be damaged by water

event of a spill, place your tower well away from electrical devices,

Remember that your tower is a water vessel. To minimize risk in the

- The components of your tower are not dishwasher-safe.

•
outdoors may result in damage.

Your tower is designed only to be placed indoors. Placing your tower

2

3. Align the bottom of a snap-fit module with the top of the twist-lock
base module so that the foot of the upper module fits into the receiver
of the lower module, then gently push the upper module down until it


snaps snugly together with the lower module.

DRAFT

4. Repeat step 3 with the remaining planter modules.
5. Using the same method, insert the chimney module into the snap-fit

receiver of the topmost planter module.

6. Insert the water inlet of the shower head into one end of the 13mm

hose.

14

# DRAFT

## 3 Assembly Instructions – 80mm

### 3.1 Parts

1x Bucket Lid 1x Bucket lid lock-ring 1x Bucket lid cap

1x Two-wire cable

gland

1x Three-wire cable

gland

1x Twist-lock base

module

4x Snap-fit module 1x Chimney module 1x Shower head

3

### 4.2 Assembly

1. Align the arrow at the base of the twist-lock base module with the
arrow on the top of the bucket lid. Carefully insert the base of the

DRAFT; point.

aligned.

module into the hole in the center of the bucket lid when the arrows are

2. Once the twist-lock base module is inserted into the bucket lid, twist
the module clockwise until you feel it stop. Do not twist past this

13

# DRAFT

1x Chimney lid 1x 13mm hose adapter 1x 13mm Hose

1x 5L Bucket

4

DRAFT; point.

# DRAFT

1x Chimney lid 1x 13mm hose adapter 1x 13mm Hose

1x 5L Bucket

12

### 3.2 Assembly

1. Align the arrow at the base of the twist-lock base module with the
arrow on the top of the bucket lid. Carefully insert the base of the
module into the hole in the center of the bucket lid when the arrows are

aligned.

2. Once the twist-lock base module is inserted into the bucket lid, twist
the module clockwise until you feel it stop. Do not twist past this
3. Align the bottom of a snap-fit module with the top of the twist-lock

5

DRAFT; lower module, carefully push down the; fore of the upper module into

# DRAFT

### 4.1 Parts

## 4 Assembly Instructions – 50mm

1x Bucket Lid 1x Bucket lid lock-ring 1x Bucket lid cap

gland

1x Two-wire cable

gland

1x Three-wire cable

module

1x Twist-lock base

5x Snap-fit module 1x Chimney module 1x Shower head

11

base module so that the net pot receptacles of each module are facing

180 degrees away from one another.

4.
push the

With the pot receptacle of the lower module facing toward you, first

rear of the upper module down into the snap-fit receiver of

the lower module.

With the rear of the upper module seated in the snap-fit receiver of the
should seat fully into the snap-fit receiver of the lower module.

the snap-fit receiver of the lower module. The foot of the upper module

6

DRAFT

tower chimney.

10

# DRAFT

6. Repeat steps 3 through 5 with the remaining planter modules.
7. Using the same method, insert the chimney module into the snap-fit


receiver of the topmost planter module.

8. Insert the water inlet of the shower head into one end of the 13mm

hose.

9. Insert the opposite end of the 13mm hose into the tower through the

top of the chimney module, then insert the shower head into the top

of the chimney module and push it down as far as it will go. Do not

force the shower head further into the chimney module than it will go.

7

DRAFT won’t sit properly on the bucket.; same outlet, insert the 13mm end of the; 13mm hose adapter into the

# DRAFT

16. Lower the bucket lid lock-ring, with its flat side facing upward, down both thumbs.


and around to the other side in both directions simultaneously with

bucket-lid. It may be easiest to work from one point on the lock-ring

bucket lid, then carefully push the lock-ring down into place around the

over the top of the tower. Align the lock-ring with the edge of the

17. Insert the bucket lid cap, with its flat side facing upward, into the cap opening in the bucket lid.
18. Place the chimney lid, with its flat side facing upward, on top of the

9

aid the laminar flow of water over the inner wall of the tower, so

The shower head is designed to fit snugly into the chimney module to

be

careful not to angle the shower head as you insert it.

10.
adjacent to the net pot receptacles.

If needed, twist the shower head so that the hose descends the tower

11. Insert the appropriate bucket lid cable gland for your chosen pump’s
power cord into the cable gland receiver of the bucket lid. Be careful

to ensure that the cable gland is oriented correctly, or the bucket lid

12. Place your submersible pump in the 5L bucket.

13.
If using an Aqua One 103 pump or other Aqua One pump with the
adapters will need to be provided by the user.

free end of the 13mm hose. If using a different pump, appropriate

14.
pump in the bucket to ensure that the pump outlet aligns with the hose.

of the submersible pump. You may need to adjust the position of the

lip of the bucket, connect the free end of the 13mm hose to the outlet

While holding the tower so that the bucket lid hovers just above the

15.
chimney so that the hose is straightened but not taut.

bucket lid is lowered, gently pull the shower head upward inside the

cord of the pump is routed through the bucket lid cable gland. As the

Lower the bucket lid onto the lip of the bucket, ensuring that the power

8

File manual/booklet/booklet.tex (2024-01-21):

\documentclass[a4paper]{article}

\usepackage[final]{pdfpages} 

\begin{document} 

\includepdf[pages=-,landscape,signature=24]{../main.pdf}

\end{document}

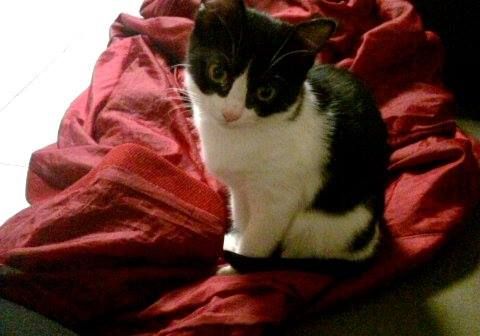
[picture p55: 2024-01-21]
manual/images/80mm/1.jpg

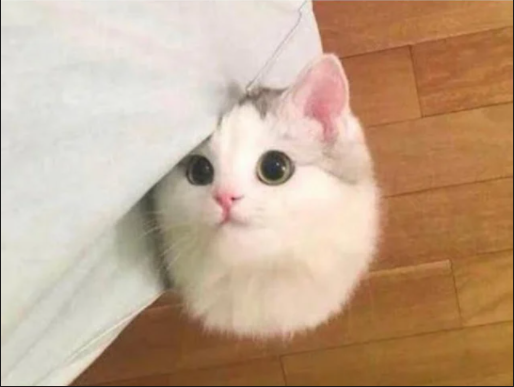
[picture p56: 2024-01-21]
manual/images/80mm/2.png

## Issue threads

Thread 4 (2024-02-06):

Compatibility Issue with 3mf Files in Prusa Slicer

Francisco-Huerta, 2024-02-06:
## Steps to Reproduce
1. Download the 3mf files from the repository.
2. Attempt to open or import the files into Prusa Slicer (2.7.0).
3. Observe that the files do not import and Prusa Slicer doesn't open.

## Expected Behavior
The 3mf files should import seamlessly into Prusa Slicer, allowing for straightforward slicing and preparation for 3D printing.

## Actual Behavior
The files do not work as expected with Prusa Slicer, causing potential barriers for users relying on this slicer for 3D printing project components.

## Workaround
I've found that importing the .step files into Autodesk Fusion 360 and then exporting them 3mf works without issues. This process suggests that there might be compatibility or formatting issues with the current 3mf files.

## Suggested Next Steps
- It might be beneficial for the project to investigate the compatibility of the current 3mf files with various slicers, particularly Prusa Slicer.
- If it's determined that the issue is widespread, consider providing alternative file formats directly in the repository to accommodate users of different slicing software.

## Offer to Help
I am willing to contribute by providing the files I've successfully converted and tested with Prusa Slicer. If this is something you are interested in, I can prepare and submit a pull request with the new files.

Thank you for considering this issue. I believe addressing it could significantly improve the accessibility and usability of the project's 3D models for a wider range of users.

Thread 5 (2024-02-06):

Proposed 50mm Shower Head Design Improvement to Reduce Clogging

Francisco-Huerta, 2024-02-06:
## Issue Description
I've identified a potential improvement to the 50mm shower head component of the hydroponic system, located in the repository. The current design has tight spaces that lead to frequent clogging, potentially affecting the system's efficiency and reliability.

## Proposed Improvement
I have developed an alternative model for the shower head that features wider spacing to mitigate the clogging issue. This modification aims to enhance the system's reliability and user experience by ensuring smoother operation.

## Details of the Modification
The new model design increases the spacing between outlets, which facilitates better water flow and reduces maintenance issues. This adjustment maintains the original functionality while improving operational reliability.

## Link to the Current Design
You can find the current shower head design here:
[Current Shower Head Model step file](https://github.com/danielle-sopalski/towers/blob/main/50mm/50mm%20Shower%20Head.step)
[Current Shower Head Model 3mf file](https://github.com/danielle-sopalski/towers/blob/main/50mm/3mf/50mm%20Shower%20Head.3mf)

## Link to the Modified Design
I've uploaded the revised model to a branch/fork of this repository. Here's the link to my proposed shower head model:
[New Shower Head Model step file](https://github.com/Francisco-Huerta/towers/blob/main/50mm/50mm%20Shower%20Head%20widerSpace.step)
[New Shower Head Model 3mf file](https://github.com/Francisco-Huerta/towers/blob/main/50mm/3mf/50mm%20Shower%20Head%20WiderSpace.3mf)

## Suggested Next Steps
- Evaluate the proposed model design for effectiveness and compatibility with the existing system.
- Consider adopting this new design in the project to improve overall functionality.
- I am available for discussions on this improvement and open to making further modifications based on feedback and testing results.

## Offer to Help
I am eager to assist with integrating this design improvement into the project and can help with adjustments, testing, and documentation as needed.

Thank you for considering this improvement. I believe the proposed modification will significantly enhance the hydroponic system's functionality and user satisfaction.

danielle-sopalski, 2024-02-06:
Hi @Francisco-Huerta! Just wanted to leave a message here to let you know that I've seen your submitted issues and pull request and that I'm keen to discuss and action them with you. I'm super excited to see someone contributing their ideas to the project. :) Thank you!

It's a busy time for me right now, and it may be a few days before I can take the time to properly look over and respond to what you've submitted.

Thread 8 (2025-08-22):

light support

kingajohanna, 2025-08-22:
hi, i’m amazed by your work! i wanna print this, but i have a question. are you planning to add light support to the design? i’ve seen this in another project, and i think it is a great idea.

https://preview.redd.it/my-hydroponic-tower-garden-3dprint-free-download-link-in-v0-huapbj9oc7hd1.jpg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

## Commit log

2024-01-21 Squash all commits into new initial commit
    [50mm Chimney Module.3mf, 50mm Chimney Module.step, 50mm Planter Base Module.3mf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]
2024-02-03 Round sharp corners of pot receptacles
    [50mm Planter Base Module.3mf, 50mm Planter Base Module.step, 50mm Planter Module.3mf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]
2024-02-11 Increase chimney lid clearance 0.0 -> 0.1mm
    [Chimney Lid.3mf, Chimney Lid.step, Tower 80mm.f3z]
2024-07-12 Remove 50mm base module baffle cone
    [50mm Planter Base Module.step]
